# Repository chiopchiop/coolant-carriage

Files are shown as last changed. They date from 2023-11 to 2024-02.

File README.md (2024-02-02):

# 🚟coolant-carriage
A computer numerical control (CNC) machine is used to cut and shape materials to form prototypes. A coolant is often used to act as a lubricant to aid a CNC machine to easily cut materials such as metals, fibreglass, high-density plastics, etc. The majority of the workload in the lab involves machining aluminium, which is work-hardening material. This necessitates the use of a coolant to promptly remove generated chips from the work area and prevent them from becoming caught in the endmill. If chips become trapped, they can mar the workpiece, alter the required cutting force, and induce chattering. The current CNC machine in the lab uses a Minimum Quantity Lubrication (MQL) system. In such systems, the amount of coolant in the airstream is set by adjusting the pressure of the coolant takeup tube. In larger industrial systems, a metering valve is used. However, this is performed using height adjustment with a manual siphon system i.e. A tube immersed in a container of 99% Isopropyl Alcohol (IPA) is hand raised to different heights to allow the coolant to flow down to the coolant jet in the CNC machine at different pressures (Figure 2-1). Feedback from CNC machine operators indicates that the manual siphon system is both inefficient and tiring, disrupting workflow and causing user fatigue. In this project, a coolant carriage will be designed to hold the container and is free to slide smoothly vertically along an aluminium V profile. 

full coolant carriage set up\
*Figure 1. Full coolant carriage set up*

### Table of contents
[Proposed idea](https://github.com/chiopchiop/coolant-carriage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)\
[Bill of materials/Assembly](https://github.com/chiopchiop/coolant-carriage#bill-of-materials-bom)\
[How to use](https://github.com/chiopchiop/coolant-carriage#how-to-use)

## Proposed idea: V slot gantry plate with carriage on three V slot aluminium profiles
Proposed idea\
*Figure 2. Initial setup vs proposed setup and the components to be designed*

## Bill of Materials (BOM)
List of components for the carriage to be 3D modelled with Fusion 360:
- V slot gantry plate to slide along the aluminium profile (Plate)
- Ratchet and pawl to move/stop carriage along the V profile (Ratchet) (Pawl)
- Carriage to hold the coolant bottle (Carriage)
- Bracket to hold the three aluminium profiles together (Bracket)
- Caps to protect against the sharp edges of the aluminium profiles (Caps)
- Bottle cap that is able to hold the siphon (Bottle cap)

STL files, quantity, and orientation of the part are in the the STL files folder

**Consolidated materials**
| Item # | Components  | Length | Qty |
| --- | --- | --- | ---|
|1 |3D printed plate |- |1 |
|2 |3D printed pawl  |- |1 |
|3 |3D printed ratchet tiles |- |2 |
|4 |3D printed carriage (backing)  |-  |1 |
|5 |3D printed carriage (clamp)  |- |1 |
|6 |3D printed bracket |- |1 |
|7 |3D printed cap 40x20 |- |1 |
|8 |3D printed cap 20x20 |- |2 |
|9 |3D printed bottle cap |- |1 |
|10 |V slot aluminium profile 40x20 |500mm |1 |
|11 |V slot aluminium profile 20x20 |203mm/8inch |2 |
|12 |M5x6x7 heat insert  |- |2 |
|13 |M5 screw |6mm |2 |
|14 |M5 screw |35mm |6 |
|15 |M5 screw |8mm |6 |
|16 |M5 roll-in nut |- |2 |
|17 |M5 spacer |8mm |2 |
|18 |M5 washer |- |4 |
|19 |M5 nut |- |4 |
|20 |M5 eccentric screw |8mm |2 |
|21 |M3x4.6x5.7 heat insert |- |2 |
|22 |M3 flathead screw |6mm |8 |
|23 |M3 screw |6mm |2 |
|24 |M3 screw |8mm |4 |
|25 |M3 roll-in nut |- |8 |
|26 |M3 Rubber feet |- |4 |
|27 |M3 roll-in nut |- |4 |

**Assembling Plate x 1**
| Item # | Components  | Length | Qty |
| --- | --- | --- | ---|
|1 |M5x6x7 heat insert |- |2 |
|2 |M5 screw |35mm |4 |
|3 |M5 spacer |8mm |2 |
|4 |M5 washer |- |4 |
|5 |M5 nut |- |4 |
|6 |M5 eccentric screw |8mm |2 |
|7 |M3x4.6x5.7 heat insert |- |2 |

\
*Figure 3. Position of heat inserts on the plate. Ignore the workmanship :grin:*

Assembly diagram_plate2\
*Figure 4. Assembling the wheels of the plate. Wheels on the left side will be fixed, while wheels on the right can be adusted with the eccentric nut*

**Assembling Ratchet Tiles x 2**
| Item # | Components  | Length | Qty |
| --- | --- | --- | ---|
|1 |M3 flathead screw |6mm |8 |
|2 |M3 roll-in nut |- |8 |

\
*Figure 5. Assembling the ratchet tiles to the aluminium profile(40x20)*

**Assembling Pawl/Hinge x 1**
| Item # | Components  | Length | Qty |
| --- | --- | --- | ---|
|1 |M3 screw |6mm |2 |

\
*Figure 6. Assembling the pawl to the plate*

**Assembling Carriage x 1**
| Item # | Components  | Length | Qty |
| --- | --- | --- | ---|
|1 |M5 screw |6mm |2 |

\
*Figure 7. Assembling the carriage to the plate*

**Assembling Bracket x 1**
| Item # | Components  | Length | Qty |
| --- | --- | --- | ---|
|1 |V slot aluminium profile 40x20 |- |1 |
|2 |V slot aluminium profile 20x20 |203mm/8inch |2 |
|3 |M5 screw |8mm |6 |
|4 |M5 screw |35mm |2 |
|5 |M5 roll-in nut |- |2 |

\
*Figure 8. Connecting the 3 aluminium profiles to the bracket with M5 screws*

**Assembling Rubber Feet**
| Item # | Components  | Length | Qty |
| --- | --- | --- | ---|
|1 |M3 Rubber feet |- |4 |
|2 |M3 screw |8mm |4 |
|3 |M3 roll-in nut |- |4 |

\
*Figure 8. Postions of the rubber feet under the aluminium profiles, using M3 screws to secure them*

\
*Figure 8. Attach caps to the edges of the aluminium profile*

Assembly diagram_finalproduct\
*Figure 8. Completed coolant carriage*

## How to use
https://youtube.com/shorts/JxCeHPnCB4s

<a href="http://www.youtube.com/watch?feature=player_embedded&v=JxCeHPnCB4s
" target="_blank">how to</a>

That concludes this project 🎺!
Special thanks to the people at Liang Research Group for the guidance and facilities! (https://liangresearch.com/)

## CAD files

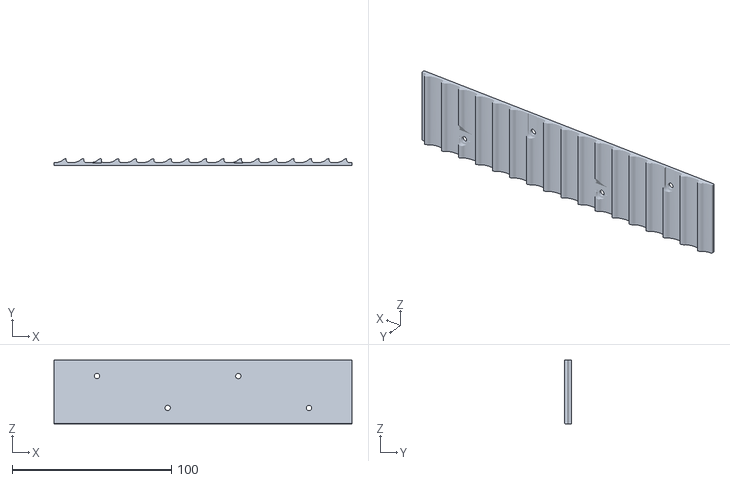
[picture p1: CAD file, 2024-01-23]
STL files/ratchet_x2.stl
187.0 x 4.16 x 40.0

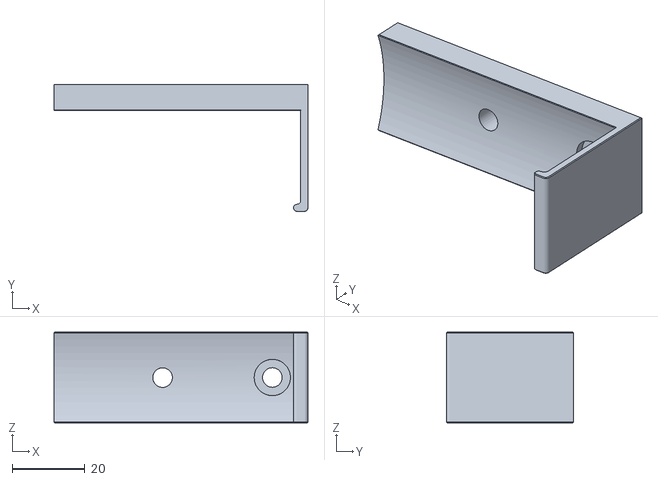
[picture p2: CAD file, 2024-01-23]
STL files/carriage backing_x1.stl
70.0 x 35.0 x 25.0

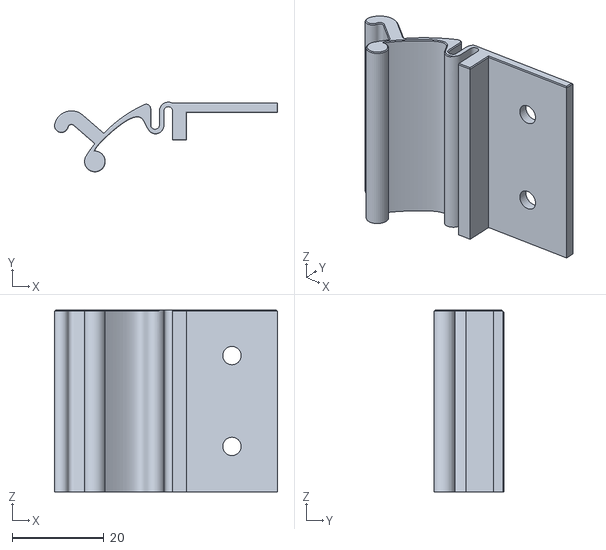
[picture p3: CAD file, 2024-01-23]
STL files/pawl_x1.stl
48.5 x 15.2 x 39.5

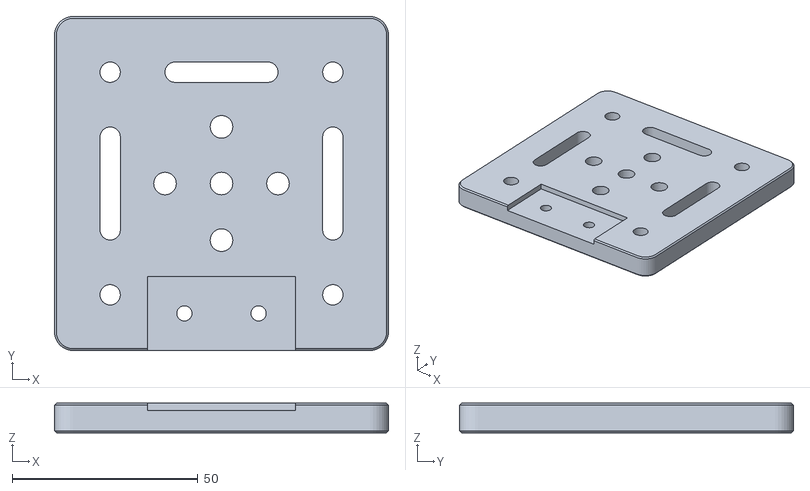
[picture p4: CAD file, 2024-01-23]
STL files/plate_x1.stl
90.0 x 90.0 x 8.00

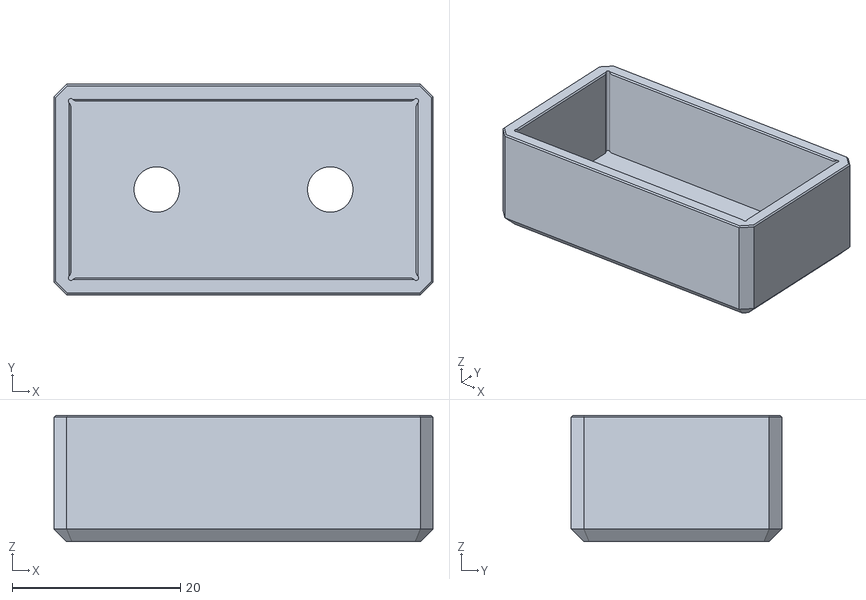
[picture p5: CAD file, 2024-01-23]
STL files/40x20cap_x1.stl
45.0 x 25.0 x 15.0

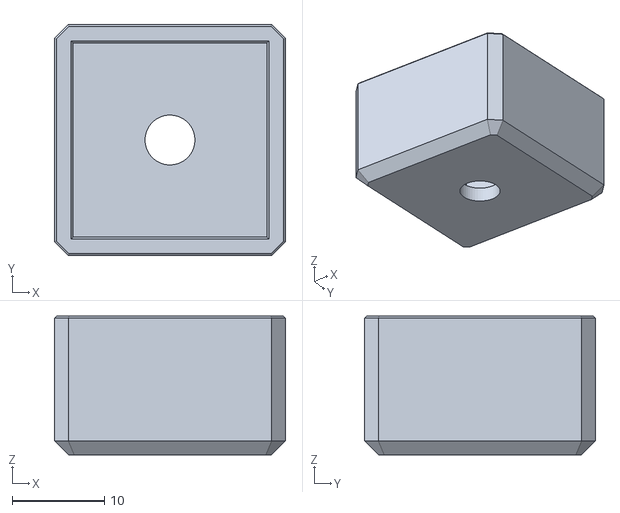
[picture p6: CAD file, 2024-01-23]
STL files/20x20cap_x2.stl
25.0 x 25.0 x 15.0

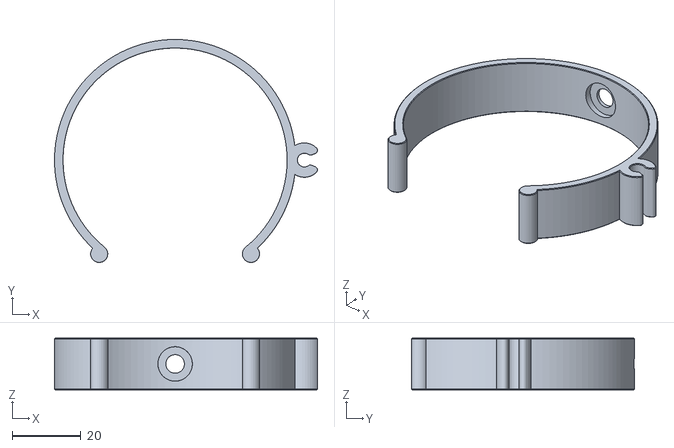
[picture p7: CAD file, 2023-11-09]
STL files/carriage holder_x1.stl
76.3 x 64.7 x 15.0

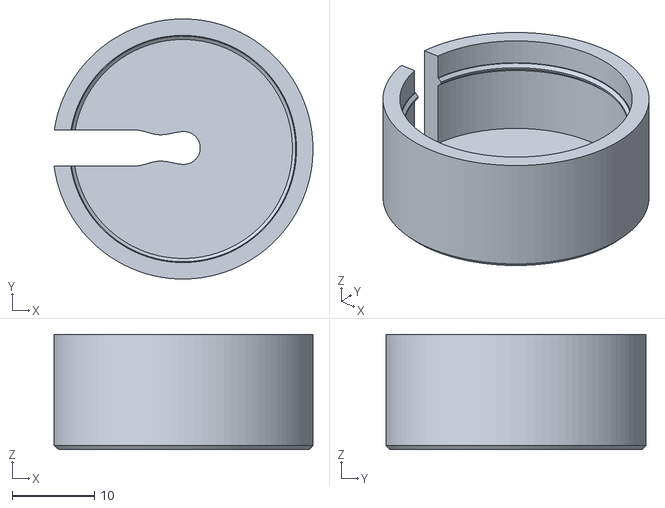
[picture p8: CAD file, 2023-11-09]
STL files/bottle cap_x1.stl
31.5 x 31.6 x 14.0

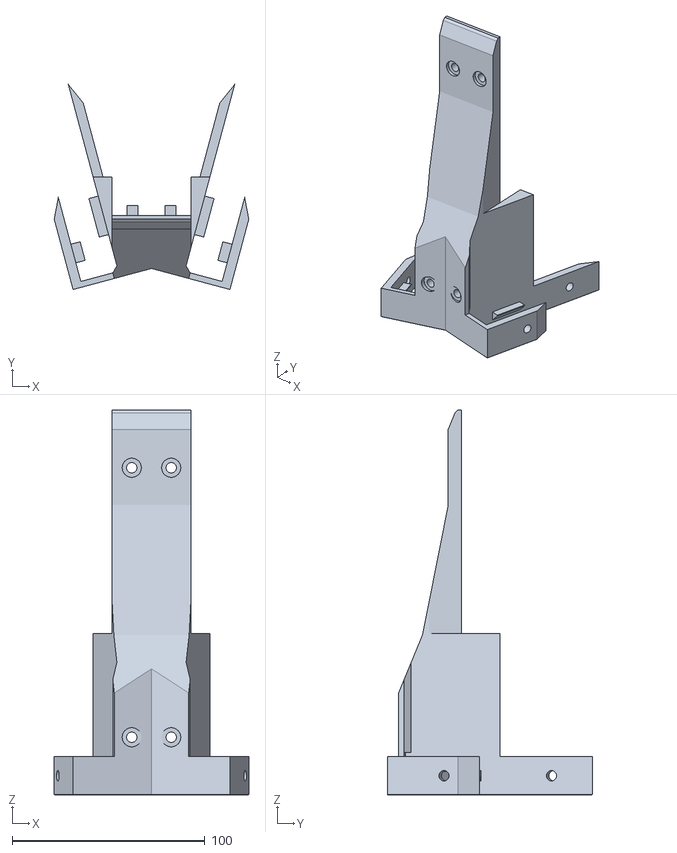
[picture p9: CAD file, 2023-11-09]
STL files/base_x1.stl
101.1 x 106.5 x 200.0

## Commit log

2023-11-09 Added stl files and printing orientation
    [bottle cap.stl, bracket.stl, cap 20x20_x2.stl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]
2024-01-23 Create STL files
